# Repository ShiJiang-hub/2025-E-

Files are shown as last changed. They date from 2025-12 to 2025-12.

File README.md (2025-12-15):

# 2025年电子设计竞赛-简易自行瞄准装置
获得该题目国一

## 项目概述
本项目为2025年全国大学生电子设计竞赛【E题简易自行瞄准装置】的完整实现方案，包含硬件设计、软件代码、调试文档等全部核心内容。
基于MSPM0系列和STM32H7系列微控制器实现了一种高精度的简易自行瞄准装置，由自动寻迹小车和二维云台激光瞄准模块组成。MSPM0G3507控制的小车通过六路红外传感器完成轨迹巡线；STM32H750同步控制云台，结合IMU姿态反馈实现反自旋，根据全局位置估计与PID控制实现动态瞄准。在基本要求中，小车可循迹绕赛道任意圈，平均每圈时间在20秒内；静止状态打靶可在2秒内使激光击中靶心（误差≤1.5cm），云台随机朝向状态打靶可在4秒内完成瞄准（误差≤1.8cm）。在发挥部分中，小车可行驶2圈同时连续瞄准靶心，激光光斑与靶心最大误差≤8cm。本设计的创新点在于融合IMU姿态稳定与运动学补偿算法，显著提升了小车在循迹过程中云台的动态瞄准精度。

## 一、硬件清单
| 模块类型 | 具体型号/规格 | 备注 |
|---|---|---|
| 主控芯片 | STM32H750+MSPM0G3507+树莓派B3+ESP32S3LDC触摸屏| 核心控制单元 |
| 电机驱动模块 | AT8236H桥驱动板 + 张大头步进电机F103驱动板x2 | 驱动直流电机+云台步进|
| 执行机构 | 直流减速电机（MG513XL）x2 + 张大头步进电机x2 |  小车四轮驱动 |
| 传感器 | 红外循迹模块（6路）+ 亚博USB免驱动摄像头 | 环境感知 |
| 电源 | 12V锂电池（2000mAh）+5V降压模块 | 供电 |
| 其他配件 | 小车底盘/编码器/ESP01s若干（组网通信） | 测速/无线控制 |

## 二、软件环境
- 开发工具：Clion（STM32，ESP32S3） / vscode+platformio（ESP01s） / CCS（MSPM0G3507）
- 依赖库：
  - STM32：HAL库
  - ESP32S3：ESPIDF
  - ESP01s：arduino

## 三、代码结构

## 四、核心功能说明
### 1. 循迹功能
- 采用6路红外传感器采集地面黑白线信号；
- 归一化+权重和处理出偏移量数据；
- 通过偏移量数据，结合循迹PID算法调整左右电机转速，实现自动循迹；

### 2. 锁定功能
- 树莓派挂载摄像头；
- 通过仿射变换+参数调整得出靶心和摄像头中心距离
- 输入系数抵消靶心距离和激光笔中心距离
- STM32H750接收该距离，通过云台PID锁定，Can通讯控制步进电机驱动器，进而控制步进电机变换角度，实现锁定靶心。

### 3. 全局补偿算法
- **补偿算法1：**小车行进过程中全程记录编码器的数值，<u>处理出行进距离和速度</u>，速度用于速度环控制小车恒速，行进距离用于构建全局坐标系，理想情况下，在一条直线上行驶，不依赖云台pid，通过计算得出云台所需要的角度和行驶在线上的距离之间的函数表达式，**对该函数求导**，得出云台的角速度；
- **补偿算法2：**小车拐弯时，陀螺仪同步有一个角速度，此时对云台输入一个反向的角速度，就能实现小陀螺算法，即旋转小车，云台保持方向不变。（陀螺仪和云台的周期不同，导致角速度不同，预处理系数解决）；

### 4.中控台调参
- ESP32S3LCD屏幕+LVGL设计中控台页面；
- 拥有PID远程调参页面，支持同时修改双环PID的六个参数；**大幅提高**PID调参效率，比赛过程中**3分钟完成一个PID环的参数整定**。
- 拥有指令页面，可操作小车进行循迹或打靶；

### 5.无线调试
- ESPNow组网：中控台+小车挂载ESP01s+树莓派挂载ESP01s；
- 树莓派将激光笔中心和摄像头中心距离发送至串口，ESP01s接收串口信息，发送至小车的ESP01s用于云台锁定以及中控台用于参数调试；
- 中控台将参数/指令发送至小车ESP01s用于参数整定；
- 所有ESP的数据发送至另外一块ESP01s（以下简称电脑ESP01s），电脑ESP01s通过USB转TTL插入电脑，选择某一台设备后，可以观察该设备的参数信息；
- ESPNow协议运行在MAC层，省去了上层协议转换所需要的实现，具体延时在1ms以内，在传输小型参数数据的延时，稳定性以及性能上远超UDP协议；

## 五、使用步骤
### 1. 硬件接线（CubeMx+CCS需按实际修改，这里不给出）

### 2. 代码烧录

### 3. 调试注意事项
- 先接电源再烧录代码，避免传感器误触发；
- 红外传感器需提前校准：vofa+查看数据，电脑ESP01s选择小车ESP01s通道观察原始数据，将小车在跑道引导线上垂直移动，利用vofa+的波形图，将每个通道的最低值和最大值写入数组，用于归一化；
- PID参数调试：先用中控台调循迹保证小车正常运动，接着让小车静止，调云台锁定靶心。最后一起联调，有补偿算法的作用下，云台pid不需要太过激进。

## 六、演示效果
- 循迹测试：小车可稳定循迹宽度≥2cm的黑色引导线，无明显偏移；
- 锁定测试：随机把摄像头摆放在某个位置，能在4s内找到靶子，并指向靶心；
- 视频链接：[小车运行演示](https://b23.tv/6O1KHSb)

## 七、常见问题解决
1. 电机不转：检查电源接线/驱动模块使能端（ENA）是否拉高；
2. 无法循迹：重新校准红外传感器阈值/输出偏移量数据到电脑ESP01s观察数据正确与否；

## 八、免责声明
本项目仅用于电子设计竞赛学习交流，请勿用于商业用途；硬件接线需严格按照说明，避免短路损坏模块。

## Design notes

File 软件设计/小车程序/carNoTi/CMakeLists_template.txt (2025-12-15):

#此文件从模板自动生成! 请勿更改!
set(CMAKE_SYSTEM_NAME Generic)
set(CMAKE_SYSTEM_VERSION 1)
cmake_minimum_required(VERSION 3.29)

# specify cross-compilers and tools
set(CMAKE_C_COMPILER arm-none-eabi-gcc)
set(CMAKE_CXX_COMPILER arm-none-eabi-g++)
set(CMAKE_ASM_COMPILER  arm-none-eabi-gcc)
set(CMAKE_AR arm-none-eabi-ar)
set(CMAKE_OBJCOPY arm-none-eabi-objcopy)
set(CMAKE_OBJDUMP arm-none-eabi-objdump)
set(SIZE arm-none-eabi-size)
set(CMAKE_TRY_COMPILE_TARGET_TYPE STATIC_LIBRARY)

# project settings
project(carNoTi C CXX ASM)
set(CMAKE_CXX_STANDARD 17)
set(CMAKE_C_STANDARD 11)

#Uncomment for hardware floating point
add_compile_definitions(ARM_MATH_CM4;ARM_MATH_MATRIX_CHECK;ARM_MATH_ROUNDING)
add_compile_options(-mfloat-abi=hard -mfpu=fpv4-sp-d16)
add_link_options(-mfloat-abi=hard -mfpu=fpv4-sp-d16)

#Uncomment for software floating point
#add_compile_options(-mfloat-abi=soft)

add_compile_options(-mcpu=cortex-m7 -mthumb -mthumb-interwork)
add_compile_options(-ffunction-sections -fdata-sections -fno-common -fmessage-length=0)

# uncomment to mitigate c++17 absolute addresses warnings
#set(CMAKE_CXX_FLAGS "${CMAKE_CXX_FLAGS} -Wno-register")

# Enable assembler files preprocessing
add_compile_options($<$<COMPILE_LANGUAGE:ASM>:-x$<SEMICOLON>assembler-with-cpp>)

if ("${CMAKE_BUILD_TYPE}" STREQUAL "Release")
    message(STATUS "Maximum optimization for speed")
    add_compile_options(-Ofast)
elseif ("${CMAKE_BUILD_TYPE}" STREQUAL "RelWithDebInfo")
    message(STATUS "Maximum optimization for speed, debug info included")
    add_compile_options(-Ofast -g)
elseif ("${CMAKE_BUILD_TYPE}" STREQUAL "MinSizeRel")
    message(STATUS "Maximum optimization for size")
    add_compile_options(-Os)
else ()
    message(STATUS "Minimal optimization, debug info included")
    add_compile_options(-Og -g)
endif ()

include_directories(Core/Inc
        Drivers/STM32H7xx_HAL_Driver/Inc
        Drivers/STM32H7xx_HAL_Driver/Inc/Legacy
        Drivers/CMSIS/Device/ST/STM32H7xx/Include
        Drivers/CMSIS/Include Middlewares/Third_Party/FreeRTOS/Source/include
        Middlewares/Third_Party/FreeRTOS/Source/CMSIS_RTOS_V2
        Middlewares/Third_Party/FreeRTOS/Source/portable/GCC/ARM_CM4F
        SYS/H)

add_definitions(-DDEBUG -DUSE_PWR_LDO_SUPPLY -DUSE_HAL_DRIVER -DSTM32H750xx)

file(GLOB_RECURSE SOURCES "Core/*.*" "Middlewares/*.*" "Drivers/*.*" "SYS/*.*")

set(LINKER_SCRIPT ${CMAKE_SOURCE_DIR}/STM32H750VBTX_FLASH.ld)

add_link_options(-Wl,-gc-sections,--print-memory-usage,-Map=${PROJECT_BINARY_DIR}/${PROJECT_NAME}.map)
add_link_options(-mcpu=cortex-m7 -mthumb -mthumb-interwork)
add_link_options(-T ${LINKER_SCRIPT})

add_executable(${PROJECT_NAME}.elf ${SOURCES} ${LINKER_SCRIPT})

set(HEX_FILE ${PROJECT_BINARY_DIR}/${PROJECT_NAME}.hex)
set(BIN_FILE ${PROJECT_BINARY_DIR}/${PROJECT_NAME}.bin)

add_custom_command(TARGET ${PROJECT_NAME}.elf POST_BUILD
        COMMAND ${CMAKE_OBJCOPY} -Oihex $<TARGET_FILE:${PROJECT_NAME}.elf> ${HEX_FILE}
        COMMAND ${CMAKE_OBJCOPY} -Obinary $<TARGET_FILE:${PROJECT_NAME}.elf> ${BIN_FILE}
        COMMENT "Building ${HEX_FILE}
Building ${BIN_FILE}")

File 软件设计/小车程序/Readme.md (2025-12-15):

carNoTi是基于stm32H750的通过Can通信控制云台的程序。
carTi是基于MSPM0G3507的控制小车循迹的程序

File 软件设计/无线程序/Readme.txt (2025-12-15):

三个esp01s，一个挂载在小车，一个挂载在树莓派，一个挂载在电脑，远程监视。
一个基于esp32s3的中控台，搭配LVGL进行参数调试。
**先把所有设备的MAC地址确定**

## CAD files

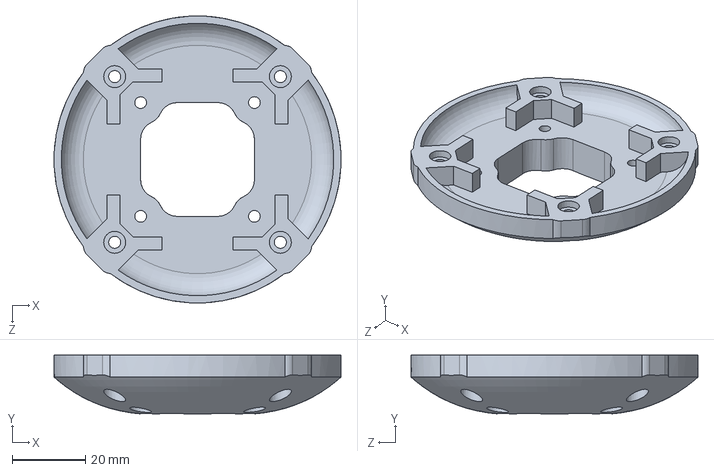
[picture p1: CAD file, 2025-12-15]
硬件设计/打印件3D模型/简易底配铜柱.SLDPRT
78.2 x 16.0 x 78.2 mm

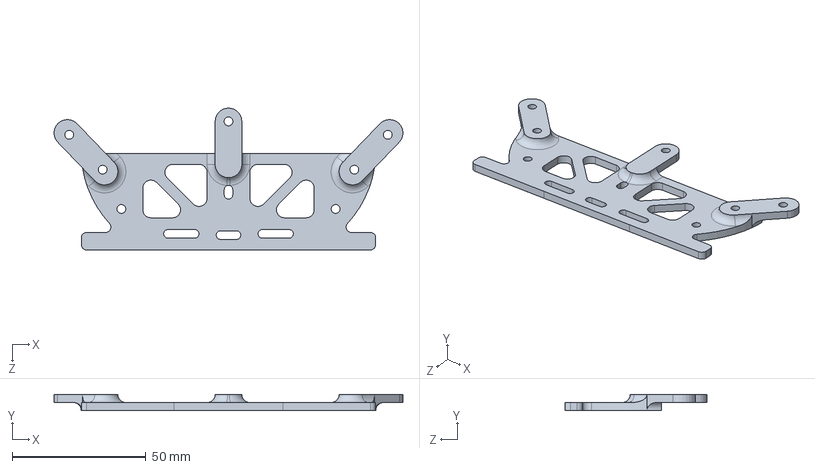
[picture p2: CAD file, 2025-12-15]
硬件设计/打印件3D模型/红外支架.SLDPRT
130.4 x 6.00 x 53.0 mm

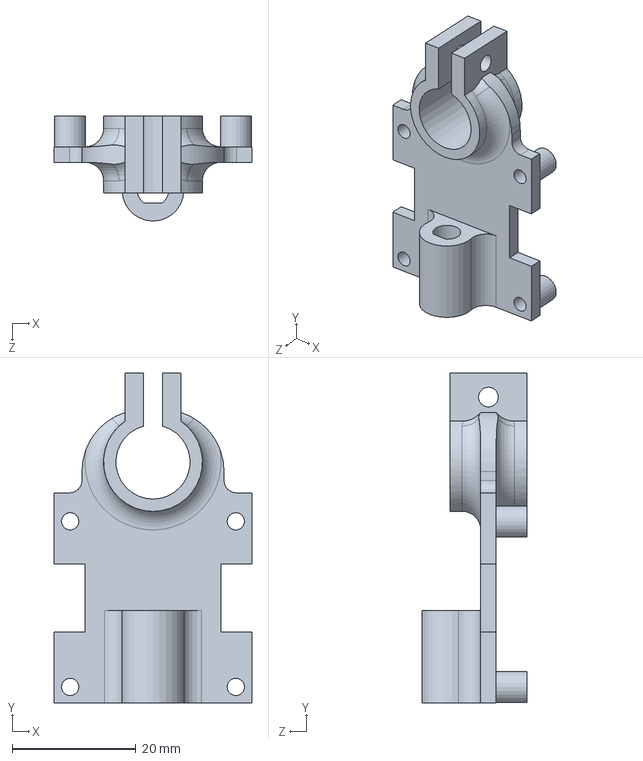
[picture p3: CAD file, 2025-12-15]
硬件设计/打印件3D模型/激光合摄像头.SLDPRT
32.0 x 53.4 x 17.0 mm

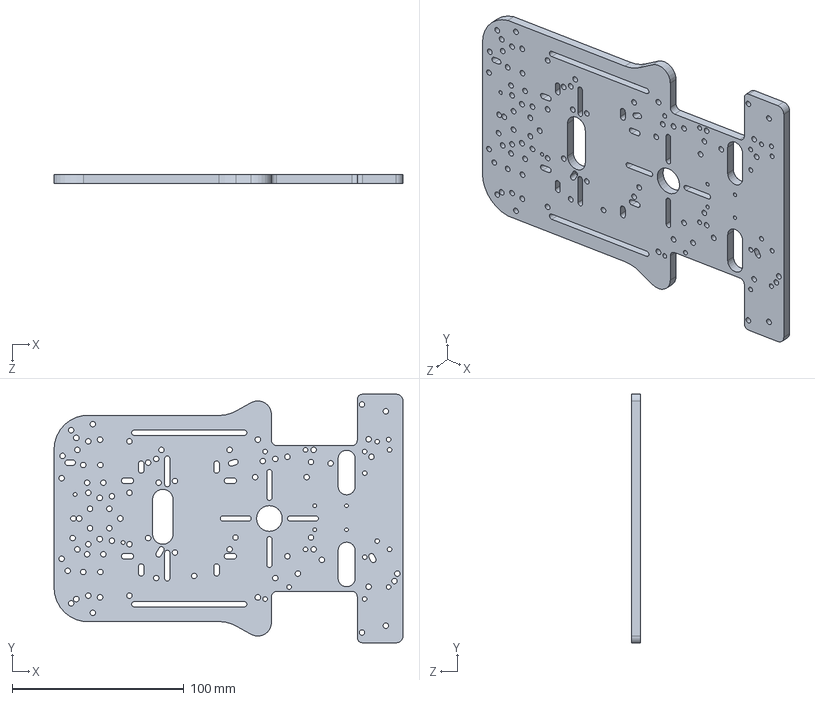
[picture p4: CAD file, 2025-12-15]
硬件设计/打印件3D模型/车底板MG513x.SLDPRT
203.5 x 145.0 x 5.00 mm

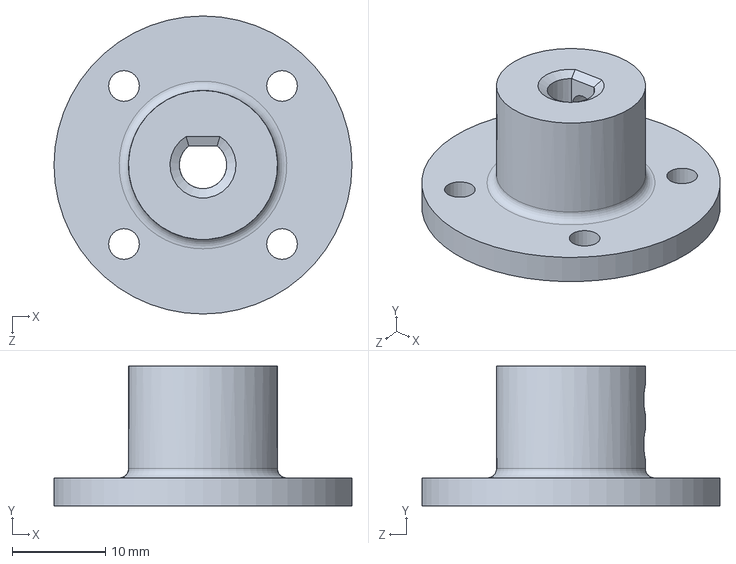
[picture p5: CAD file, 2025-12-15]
硬件设计/打印件3D模型/简易法兰盘5mm.SLDPRT
32.0 x 15.0 x 32.0 mm

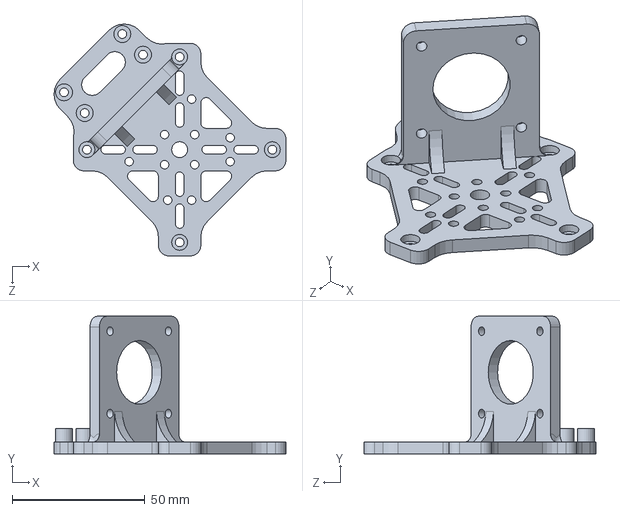
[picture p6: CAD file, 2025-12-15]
硬件设计/打印件3D模型/简易底板上.SLDPRT
87.2 x 51.8 x 87.2 mm

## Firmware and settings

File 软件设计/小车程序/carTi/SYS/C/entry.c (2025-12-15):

#include "stdio.h"
#include "string.h"
#include "entry.h"
#include "dataRead.h"
#include "control.h"
#include "Trace.h"

char sendmsg[64];
uint8_t Serial_buf[64];
int result;
int num1=0,num2=0;
Car_t myCar;
Car_t targetCar;
//临时测试
int speed = 15;
Position_t nowPosition;
uint8_t lastCarState;
 uint8_t test;
void pidTest();
int32_t lastWakeTime;
int32_t globatime;

void setup(){
        
        //  NVIC_ClearPendingIRQ(TOF_INST_INT_IRQN);
        // NVIC_EnableIRQ(TOF_INST_INT_IRQN);
        NVIC_EnableIRQ(GPIOB_INT_IRQn);
        NVIC_EnableIRQ(GPIOA_INT_IRQn);
        DL_ADC12_startConversion(ADC_INST);
        PID_Init();
        
        DL_GPIO_setPins(myShow_PORT, myShow_LED_PIN);
        myCar.carState = Car_Stop;
        NVIC_EnableIRQ(TIMER_0_INST_INT_IRQN);
    }

void loop(){
    //  DL_GPIO_togglePins(myShow_PORT, myShow_LED_PIN);
    //  sprintf(sendmsg,"%d,%d,%d,%d\r\n",leftMotor.speed,leftMotor.motoCount,rightMotor.motoCount,rightMotor.motoCount);
    keyScan();
    if(Serial_RxFlag){
         pidTest();
         //Position_DataRead(Serial_buf,&num1,&num2);
        Serial_RxFlag = 0;
    }
    // if(YunTaiOKFlag){
    //     if(DL_GPIO_readPins(myShow_PORT,myShow_YunTai_PIN)){
    //         myCar.carState = Car_Trace;
    //     }
    // }
    test = (DL_GPIO_readPins(ccd_PORT,ccd_YunTai_PIN)>>28)&0x01;
    if(YunTaiOKFlag){
        if(test==1){
            myCar.carState = Car_Trace;
            YunTaiOKFlag = 0;
        }
    }
    //sprintf(sendmsg,"%d,%d\r\n",num1,num2);
    //  sprintf(sendmsg,"%d,%d,%d,%d\r\n",num1,num2,leftMotor.speed,rightMotor.speed);
    // sprintf(sendmsg,"@TI:%d,%d,%d,%d,%d]%%\r\n",leftMotor.motoCount,rightMotor.motoCount,leftMotor.speed,rightMotor.speed,myCar.hasTurn);
  //sprintf(sendmsg,"%.3f,%.3f,%.3f\r\n",PID_Trace.Kp,PID_Trace.Ki,PID_Trace.Kd);
    // sprintf(sendmsg,"%d,%d,%d,%.2f\r\n",myCar.carState,globatime,lastWakeTime,inf_std);
    // Load(num1,num2);
    // sprintf(sendmsg,"%.2f,%d\r\n",inf_std,myCar.carState);
    sprintf(sendmsg,"@TI:%d,%d,%d,%d,%d,%d]%%\r\n",leftMotor.motoCount,rightMotor.motoCount,leftMotor.speed,rightMotor.speed,myCar.hasTurn,YunTaiMode);
    uart0_send_string(TOF_INST, sendmsg);
    DL_GPIO_togglePins(mosSW_PORT, mosSW_mos1_PIN);
    DL_GPIO_togglePins(mosSW_PORT, mosSW_mos2_PIN);
    delay_ms(15);
}

void TIMG0_IRQHandler(void){
    static int timeslice = 0;
    globatime++;
    inf_Read();
    speedUpdate();
    if(myCar.carState!=Car_Stop){
        if(myCar.carState==Car_Trace){
            timeslice++;
            if(timeslice>3){
                speed++;
                if(speed>16) speed = 16;
                timeslice = 0;
            }
            Trace_Black(inf_std, speed, &PID_Trace);
            leftMotor.motoCount += leftMotor.speed;
            rightMotor.motoCount += rightMotor.speed;
            if(inf_std<=210&&(globatime-lastWakeTime)>200){//转弯
            // 进入转弯状态
                myCar.carState = Car_Turn;
                lastWakeTime = globatime;
                if(myCar.hasTurn % 4 == 0&&myCar.hasTurn!=0) {
                myCar.CircleNum++;
                // 达到目标圈数，停止
                if(myCar.CircleNum >= targetCar.CircleNum) {
                    myCar.carState = Car_Stop;
                    myCar.hasTurn = 0;  // 重置转弯计数
                    myCar.CircleNum = 0; // 重置圈数计数
                    targetCar.CircleNum = 0;// 重置目标圈数
                    sprintf(sendmsg,"@TraceOK%%\r\n");
                    uart0_send_string(TOF_INST, sendmsg); 
                    DL_TimerA_setCaptureCompareValue(carPWM_INST, (uint32_t)0, DL_TIMER_CC_0_INDEX);
                    DL_TimerA_setCaptureCompareValue(car1N_INST, (uint32_t)10, DL_TIMER_CC_1_INDEX);
                    DL_TimerA_setCaptureCompareValue(carPWM_INST, (uint32_t)10, DL_TIMER_CC_1_INDEX);
                    DL_TimerA_setCaptureCompareValue(car2N_INST, (uint32_t)0, DL_TIMER_CC_0_INDEX);

                }
                }
            }
        }
        else if(myCar.carState == Car_Turn){
            timeslice++;
            speed = 2;
            Trace_Black(inf_std, speed, &PID_Turn);
            if(timeslice==30){
                leftMotor.motoCount = 0;
                rightMotor.motoCount = 0;
            }
            if(timeslice>=30&&inf_std>=230){
                timeslice = 0;
                DL_GPIO_togglePins(myShow_PORT, myShow_LED_PIN);
                myCar.hasTurn++;
                myCar.carState = Car_Trace;
            }
        }
    }
}
void GROUP1_IRQHandler(void){
    switch(DL_Interrupt_getPendingGroup(DL_INTERRUPT_GROUP_1)){
        case DL_INTERRUPT_GROUP1_IIDX_GPIOA:
            encoderFunctionA();
            break;
        case DL_INTERRUPT_GROUP1_IIDX_GPIOB:
            encoderFunctionB();
            break;
        default:
            break;
    }

}

void delay_ms(unsigned long ms) 
{
    while(ms--)
	    delay_cycles(CPUCLK_FREQ/1000);
}
void pidTest(){
    if(strncmp((char*)Serial_buf,"PosKp",5) == 0) {//控制pid
        int num_args = 1;
        int temp = 0;
        Position_DataRead(Serial_buf,&temp,&num_args);
        PID_Trace.Kp = temp / 1000.0f;
    }else if(strncmp((char*)Serial_buf,"PosKi",5) == 0) {
        int num_args = 1;
        int temp = 0;
        Position_DataRead(Serial_buf,&temp,&num_args);
        PID_Trace.Ki = temp/100.0;
    }else if(strncmp((char*)Serial_buf,"PosKd",5) == 0) {
        int num_args = 1;
        int temp = 0;
        Position_DataRead(Serial_buf,&temp,&num_args);
        PID_Trace.Kd = temp/100.0f;
    }else if(strncmp((char *)Serial_buf, "[", 1)==0){
        Position_DataRead(Serial_buf,&num1,&num2);
    }else if(strncmp((char *)Serial_buf,"OK",2)==0){
        if(YunTaiOKFlag){
            myCar.carState = Car_Trace;
            YunTaiOKFlag = 0;
        }
    }
}

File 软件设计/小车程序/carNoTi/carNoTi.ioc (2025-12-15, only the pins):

Mcu.UserName=STM32H750VBTx
PA0.GPIO_Label=PWM1
PA0.Signal=S_TIM2_CH1_ETR
PA1.GPIO_Label=PWM2
PA1.Signal=S_TIM2_CH2
PA11.Signal=UART4_RX
PA12.Signal=UART4_TX
PA6.GPIO_Label=E1A
PA6.Signal=S_TIM3_CH1
PA7.GPIO_Label=E1B
PA7.Signal=S_TIM3_CH2
PB0.GPIO_Label=ccd_si
PB0.Signal=GPIO_Output
PB10.GPIO_Label=PWM3
PB10.Signal=S_TIM2_CH3
PB11.GPIO_Label=PWM4
PB11.Signal=S_TIM2_CH4
PB12.Signal=FDCAN2_RX
PB13.Signal=FDCAN2_TX
PB6.Signal=I2C1_SCL
PB7.Signal=I2C1_SDA
PC0.Signal=GPIO_Output
PC1.Signal=GPIO_Output
PC13.GPIO_Label=Key3
PC13.Signal=GPIO_Input
PC2_C.Signal=GPIO_Output
PC4.Signal=ADCx_INP4
PC5.GPIO_Label=ccd_clk
PC5.Signal=GPIO_Output
PD10.GPIO_Label=Key2
PD10.Signal=GPIO_Input
PD11.GPIO_Label=Key1
PD11.Signal=GPIO_Input
PD12.GPIO_Label=E2A
PD12.Signal=S_TIM4_CH1
PD13.GPIO_Label=E2B
PD13.Signal=S_TIM4_CH2
PD15.GPIO_Label=Buzzer
PD15.Signal=GPIO_Output
PD7.GPIO_Label=YunTaiOk
PD7.Signal=GPIO_Output
PD8.GPIO_Label=SW2
PD8.Signal=GPIO_Output
PD9.GPIO_Label=SW1
PD9.Signal=GPIO_Output
PE11.GPIO_Label=PWMB
PE11.Signal=S_TIM1_CH2
PE13.GPIO_Label=PWMC
PE13.Signal=S_TIM1_CH3
PE14.GPIO_Label=PWMD
PE14.Signal=S_TIM1_CH4
PE4.GPIO_Label=BIN2
PE4.Signal=GPIO_Output
PE5.GPIO_Label=BIN1
PE5.Signal=GPIO_Output
PE6.GPIO_Label=AIN2
PE6.Signal=GPIO_Output
PE7.Signal=UART7_RX
PE8.Signal=UART7_TX
PE9.GPIO_Label=PWMA
PE9.Signal=S_TIM1_CH1

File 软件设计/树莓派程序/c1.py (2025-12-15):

import cv2
import numpy as np
import serial
import time
from jiaozheng import CameraCalibration

# 相机校准
calibrator = CameraCalibration(r"/home/pi/Desktop/last/calibration_result.yaml")

# A4纸实际参数（厘米）
A4_WIDTH_CM = 17.1   # 短边
A4_HEIGHT_CM = 26.0  # 长边
A4_ASPECT_RATIO = A4_HEIGHT_CM / A4_WIDTH_CM  # 长宽比
ASPECT_RATIO_TOLERANCE = 0.4# 比例容忍度

# 串口配置
SERIAL_PORT = '/dev/ttyUSB0'  # Linux端口，Windows为'COM3'等
BAUD_RATE = 115200
TIMEOUT = 1


class A4RectangleDetector:
    def __init__(self):
        self.min_area = 2000  # 最小面积阈值
        self.max_area = 80000  # 最大面积阈值
        self.contour_epsilon = 0.1  # 轮廓近似系数
        self.angle_threshold = 70  # 矩形角阈值（接近直角）
        self.last_center = None  # 上一次原图中心点
        self.pixels_per_cm = None  # 像素/厘米比例
        self.detected_area = 0  # 检测到的面积
        self.warped = None  # 透视变换后的正视图
        self.warped_center = None  # 正视图中的中心
        # 正视图尺寸（与A4比例一致）
        self.target_width = 171  # 对应短边
        self.target_height = 260  # 对应长边

    def _order_points(self, pts):
        """顺时针排序角点（左上->右上->右下->左下）"""
        s = pts.sum(axis=1)
        diff = np.diff(pts, axis=1)
        top_left = pts[np.argmin(s)]
        bottom_right = pts[np.argmax(s)]
        top_right = pts[np.argmax(diff)]
        bottom_left = pts[np.argmin(diff)]
        return np.array([top_left, top_right, bottom_right, bottom_left], dtype="float32")

    def _is_rectangle(self, approx):
        """判断是否为矩形（检查直角）"""
        if len(approx) != 4:
            return False
            
        corners = approx.reshape(4, 2).astype(np.float32)
        vectors = []
        for i in range(4):
            p1 = corners[i]
            p2 = corners[(i+1)%4]
            vectors.append(p2 - p1)
            
        # 检查每个角是否为直角
        for i in range(4):
            v1 = vectors[i]
            v2 = vectors[(i+1)%4]
            dot = np.dot(v1, v2)
            norm1 = np.linalg.norm(v1)
            norm2 = np.linalg.norm(v2)
            
            if norm1 == 0 or norm2 == 0:
                return False
                
            cos_theta = abs(dot / (norm1 * norm2))
            cos_theta = np.clip(cos_theta, 0.0, 1.0)
            angle = np.arccos(cos_theta) * 180 / np.pi
            
            if angle < self.angle_threshold:
                return False
        return True

    def _check_aspect_ratio(self, corners):
        """检查矩形长宽比是否接近A4纸"""
        # 计算相邻两边的长度（矩形的宽和长）
        side1 = np.linalg.norm(corners[0] - corners[1])  # 边1长度
        side2 = np.linalg.norm(corners[1] - corners[2])  # 边2长度
        
        # 计算长宽比（长边/短边）
        if side1 > side2:
            aspect_ratio = side1 / side2
        else:
            aspect_ratio = side2 / side1
            
        # 检查是否在A4比例的容忍范围内
        min_ratio = A4_ASPECT_RATIO * (1 - ASPECT_RATIO_TOLERANCE)
        max_ratio = A4_ASPECT_RATIO * (1 + ASPECT_RATIO_TOLERANCE)
        return min_ratio <= aspect_ratio <= max_ratio

    def _calculate_pixel_ratio(self, corners):
        """计算像素/厘米比例"""
        p1, p2, p3, p4 = corners
        width_pixels = np.linalg.norm(p1 - p2)  # 短边像素长度
        height_pixels = np.linalg.norm(p2 - p3)  # 长边像素长度
        
        ratio_width = width_pixels / A4_WIDTH_CM
        ratio_height = height_pixels / A4_HEIGHT_CM
        return (ratio_width + ratio_height) / 2  # 平均比例

    def _perspective_transform(self, corners):
        """计算透视变换矩阵并生成正视图"""
        # 目标正视图的四个角点（左上、右上、右下、左下）
        target_corners = np.array([
            [0, 0],
            [self.target_width - 1, 0],
            [self.target_width - 1, self.target_height - 1],
            [0, self.target_height - 1]
        ], dtype="float32")
        # 计算透视变换矩阵
        M = cv2.getPerspectiveTransform(corners, target_corners)
        # 生成正视图（使用原图彩色图，便于观察）
        self.warped = cv2.warpPerspective(
            self.original_frame,  # 用彩色原图生成正视图
            M, 
            (self.target_width, self.target_height)
        )
        # 计算逆变换矩阵（用于将正视图中心映射回原图）
        self.M_inv = cv2.getPerspectiveTransform(target_corners, corners)
        # 正视图中心（物理中心）
        self.warped_center = (self.target_width // 2, self.target_height // 2)
        return self.warped_center

    def _get_original_center(self):
        """将正视图中心映射回原图，得到原图中的真实中心"""
        if self.warped_center is None or not hasattr(self, 'M_inv'):
            return None
        # 正视图中心坐标
        warped_center_np = np.array([[self.warped_center]], dtype="float32")
        # 映射回原图
        original_center = cv2.perspectiveTransform(warped_center_np.reshape(-1, 1, 2), self.M_inv)
        return (int(original_center[0][0][0]), int(original_center[0][0][1]))

    def detect_and_draw(self, frame):
        """检测符合A4比例的矩形，计算中心并绘制"""
        self.original_frame = frame.copy()  # 保存彩色原图用于透视变换
        self.original_gray = cv2.cvtColor(frame, cv2.COLOR_BGR2GRAY)
        blur = cv2.bilateralFilter(self.original_gray, 9, 75, 75)
        edges = cv2.Canny(blur, 50, 150)
        
        # 获取所有轮廓及层级关系
        contours, hierarchy = cv2.findContours(edges, cv2.RETR_TREE, cv2.CHAIN_APPROX_SIMPLE)
        
        result = frame.copy()
        min_area = self.max_area
        min_rect_corners = None
        self.detected_area = 0
        self.warped = None  # 重置正视图
        self.warped_center = None  # 重置正视图中心

        # 筛选符合条件的矩形（支持单轮廓或内轮廓）
        for i, cnt in enumerate(contours):
            area = cv2.contourArea(cnt)
            if area < self.min_area or area > self.max_area:
                continue
                
            perimeter = cv2.arcLength(cnt, True)
            approx = cv2.approxPolyDP(cnt, self.contour_epsilon * perimeter, True)
            
            # 检查是否为矩形
            if not self._is_rectangle(approx):
                continue
                
            # 检查长宽比
            corners = approx.reshape(4, 2).astype(np.float32)
            if not self._check_aspect_ratio(corners):
                continue
                
            # 角点排序
            ordered_corners = self._order_points(corners)
                
            # 优先选择面积较小的（更可能是内矩形）
            if area < min_area:
                min_area = area
                min_rect_corners = ordered_corners
                self.detected_area = area

        # 处理检测到的矩形
        original_center = None  # 原图中的矩形中心
        if min_rect_corners is not None:
            # 透视变换：生成正视图并计算中心
            self._perspective_transform(min_rect_corners)
            # 将正视图中心映射回原图
            original_center = self._get_original_center()
            self.last_center = original_center  # 保存原图中心
            
            self.pixels_per_cm = self._calculate_pixel_ratio(min_rect_corners)
            
            # 在原图上绘制检测到的矩形
            cv2.polylines(result, [min_rect_corners.astype(np.int32)], True, (0, 0, 255), 2)

        else:
            cv2.putText(result, "No inner rectangle found", (10, 30),
                       cv2.FONT_HERSHEY_SIMPLEX, 0.8, (0, 0, 255), 2)
            self.last_center = None
            self.pixels_per_cm = None
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

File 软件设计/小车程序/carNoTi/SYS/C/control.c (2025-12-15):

#include "control.h"

#include <stdio.h>
#include <stdlib.h>
#include <string.h>

#include "can_motor_control.h"
#include "dataRec.h"
#include "entry.h"
#include "main.h"
#include "task.h"
#include "usart.h"
#include "yunTaiQuestion.h"

TaskHandle_t QuestionTaskHandle;
void QuestionTask(void *argument) {
    while(1) {
        switch(myQuestion) {
            case 1://瞄准后打点
                aimToDot();
                break;
            case 2://持续瞄准打点
                aimAndDot();
                break;
            case 3://持续瞄准并画圆
                break;
            default://选了错误的题目，啥都不做
                break;
        }
        vTaskDelay(10);
    }
}

void yunTaiPositionControl(float x,float y,int speed) {
    xDrap.theta = atan(x/100.0f);
    xDrap.theta = xDrap.theta * (180.0f / M_PI);
    yDrap.theta = atan(y/100.0f);
    yDrap.theta = yDrap.theta * (180.0f / M_PI);
    PositionModeRun(0x02,4,1,speed,1,(int32_t)(-xDrap.theta*ANGLETOCLK));
    PositionModeRun(0x01,4,1,speed,1,(int32_t)(yDrap.theta*ANGLETOCLK));
}
void yunTaiVelocityControl() {
    float speedx=0;
    int speedy;
    speedx = velocityPIDCompute(&xDrap.pidvel,(float)targetPosition.xPosition,(float)nowPosition.xPosition);
    speedy = velocityPIDCompute(&yDrap.pidvel,(float)targetPosition.yPosition,(float)nowPosition.yPosition);

     speedx += myIMU.w[2]*2.4f;
    speedx += SpeedInverse*95.7f;
    sprintf(sendmsg,"%.2f,%.2f,%d,%d,%d\r\n",myCar.xPosition,myCar.yPosition,leftMotor.speed,rightMotor.speed,myCar.hasTurn);
    if(speedx < 0) {
        SpeedModeRun(0x02,0,-(int)(speedx),0);
    }else {
        SpeedModeRun(0x02,1,(int)(speedx),0);
    }
    if(speedy < 0) {
        SpeedModeRun(0x01,0,-speedy,0);
    }else {
        SpeedModeRun(0x01,1,speedy,0);
    }
}
int detectionAiming() {
    if(abs(targetPosition.xPosition-nowPosition.xPosition)<=3 && abs(targetPosition.yPosition-nowPosition.yPosition)<=3) {
        return 1;
    }
    return 0;
}
// PID控制器初始化函数
void PID_Init() {
    xDrap.pidvel.Kp = 0.532;
    xDrap.pidvel.Ki = 0.0;
    xDrap.pidvel.Kd = 1.49;
    xDrap.pidvel.output_limit = 3000.0f;

    yDrap.pidvel.Kp = -0.532;
    yDrap.pidvel.Ki = 0.0;
    yDrap.pidvel.Kd = -1.49;
    yDrap.pidvel.output_limit = 3000.0f;
}

float positionPIDCompute(PID_Controller *pid, float target,float measure) {//位置环控制，为20ms周期
    pid->error = target - measure;
    if(pid->error<10&&pid->error>-10) pid->error = 0;
    if(pid->error<50&&pid->error>-50) {
            //积分限幅
        pid->integral += (pid->error * pid->Ki);
        if (pid->integral > pid->integral_limit) pid->integral = pid->integral_limit;
        if (pid->integral < -pid->integral_limit) pid->integral = -pid->integral_limit;
    }


    float derivative = pid->error - pid->prev_error;//微分项
    pid->prev_error = pid->error;//更新上次误差
    //输出并限幅
    float positionOutput = pid->Kp * pid->error + pid->integral+ pid->Kd * derivative;
    if(positionOutput >pid->output_limit) positionOutput = pid->output_limit;
    if(positionOutput <-pid->output_limit) positionOutput = -pid->output_limit;
    //sprintf(sendmsg,"com:%.2f\r\n",pid->integral);
    HAL_UART_Transmit(&huart7,sendmsg,strlen(sendmsg),100);
    return positionOutput;
}
float velocityPIDCompute(PID_Controller *pid, float target,float measure) {
    pid->error = target - measure;
    //积分限幅
    pid->integral += pid->error;
    if (pid->integral > pid->integral_limit) pid->integral = pid->integral_limit;
    if (pid->integral < -pid->integral_limit) pid->integral = -pid->integral_limit;

    // 计算微分项并应用低通滤波
    float derivative = pid->error - pid->prev_error;
    pid->prev_error = pid->error;  // 更新上次误差
    //输出并限幅
    float velocityOutput = pid->Kp * pid->error + pid->Ki * pid->integral +  pid->Kd * derivative;
    if(velocityOutput >pid->output_limit) velocityOutput = pid->output_limit;
    if(velocityOutput <-pid->output_limit) velocityOutput = -pid->output_limit;
    // if(target==0&&abs(measure)<50) return 0;
    return velocityOutput;
}

// 闪烁状态结构体：记录当前颜色的闪烁阶段
typedef struct {
    uint8_t current_color;    // 当前正在显示的颜色（用于检测是否切换）
    uint8_t stage;            // 闪烁阶段：0=亮灯阶段，1=灭灯阶段
    TickType_t stage_start;   // 当前阶段的开始时间（用于计算是否到切换时间）
} BlinkState;

// 全局闪烁状态（初始化）
static BlinkState blink_state = {
    .current_color = NOCOLOR,
    .stage = 0,
    .stage_start = 0
};

// 定义每个颜色的闪烁参数（亮灯时间、灭灯时间，单位：ms）
typedef struct {
    uint32_t on_time;   // 亮灯时长
    uint32_t off_time;  // 灭灯时长
} BlinkParam;

// 颜色-闪烁参数映射表（与case对应）
static const BlinkParam blink_params[] = {
    [WHITE]   = {1000, 0},  // 常量
    [YELLOW]   = {1000, 1000},   // 亮2000ms，灭500ms
    [PURPLE]  = {0, 1000},    // 亮500ms，灭500ms
    [RED]     = {200, 200},    // 亮200ms，灭200ms
    [CYAN]    = {100, 400},    // 亮400ms，灭600ms
    [GREEN]   = {2000, 500},   // 亮2000ms，灭500ms
    [BLUE]    = {700, 300},    // 亮700ms，灭300ms
    [NOCOLOR] = {0, 0}         // 常灭
};
// 蜂鸣器状态：记录是否正在鸣叫及开始时间
typedef struct {
    uint8_t is_buzzing;       // 0：未鸣叫；1：正在鸣叫
    TickType_t buzz_start;    // 鸣叫开始时间（用于计算500ms）
} BuzzerState;

// 全局蜂鸣器状态（初始化）
static BuzzerState buzzer_state = {
    .is_buzzing = 0,
    .buzz_start = 0
};

// 蜂鸣器控制（用户提供的GPIO操作，假设低电平响，高电平关）
#define BUZZ_ON()  do { worningFlag = 1; } while(0)  // 响（根据实际电平调整）
#define BUZZ_OFF() do { worningFlag = 0; } while(0)  // 关

void ledColorShow(uint8_t color) {
    switch(color) {
        case 0:
            HAL_GPIO_WritePin(GPIOC,GPIO_PIN_0,0);
            HAL_GPIO_WritePin(GPIOC,GPIO_PIN_1,0);
            HAL_GPIO_WritePin(GPIOC,GPIO_PIN_2,0);
        break;
        case 1:
            HAL_GPIO_WritePin(GPIOC,GPIO_PIN_0,0);
            HAL_GPIO_WritePin(GPIOC,GPIO_PIN_1,0);
            HAL_GPIO_WritePin(GPIOC,GPIO_PIN_2,1);
            break;
        case 2:
            HAL_GPIO_WritePin(GPIOC,GPIO_PIN_0,0);
            HAL_GPIO_WritePin(GPIOC,GPIO_PIN_1,1);
            HAL_GPIO_WritePin(GPIOC,GPIO_PIN_2,0);
            break;
        case 3:
            HAL_GPIO_WritePin(GPIOC,GPIO_PIN_0,0);
            HAL_GPIO_WritePin(GPIOC,GPIO_PIN_1,1);
            HAL_GPIO_WritePin(GPIOC,GPIO_PIN_2,1);
            break;
        case 4:
            HAL_GPIO_WritePin(GPIOC,GPIO_PIN_0,1);
            HAL_GPIO_WritePin(GPIOC,GPIO_PIN_1,0);
            HAL_GPIO_WritePin(GPIOC,GPIO_PIN_2,0);
            break;
        case 5:
            HAL_GPIO_WritePin(GPIOC,GPIO_PIN_0,1);
            HAL_GPIO_WritePin(GPIOC,GPIO_PIN_1,0);
            HAL_GPIO_WritePin(GPIOC,GPIO_PIN_2,1);
            break;
        case 6:
            HAL_GPIO_WritePin(GPIOC,GPIO_PIN_0,1);
            HAL_GPIO_WritePin(GPIOC,GPIO_PIN_1,1);
            HAL_GPIO_WritePin(GPIOC,GPIO_PIN_2,0);
            break;
        case 7:
            HAL_GPIO_WritePin(GPIOC,GPIO_PIN_0,1);
            HAL_GPIO_WritePin(GPIOC,GPIO_PIN_1,1);
            HAL_GPIO_WritePin(GPIOC,GPIO_PIN_2,1);
            break;
    }
}
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

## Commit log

2025-12-15 初始化2025电赛E题-简易自行瞄准装置，上传核心代码和文档
    [calibration_result.yaml, partitions_user.csv, stm32h750b-disco.cfg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]
2025-12-15 初始化2025电赛E题-简易自行瞄准装置，上传所有代码文件
